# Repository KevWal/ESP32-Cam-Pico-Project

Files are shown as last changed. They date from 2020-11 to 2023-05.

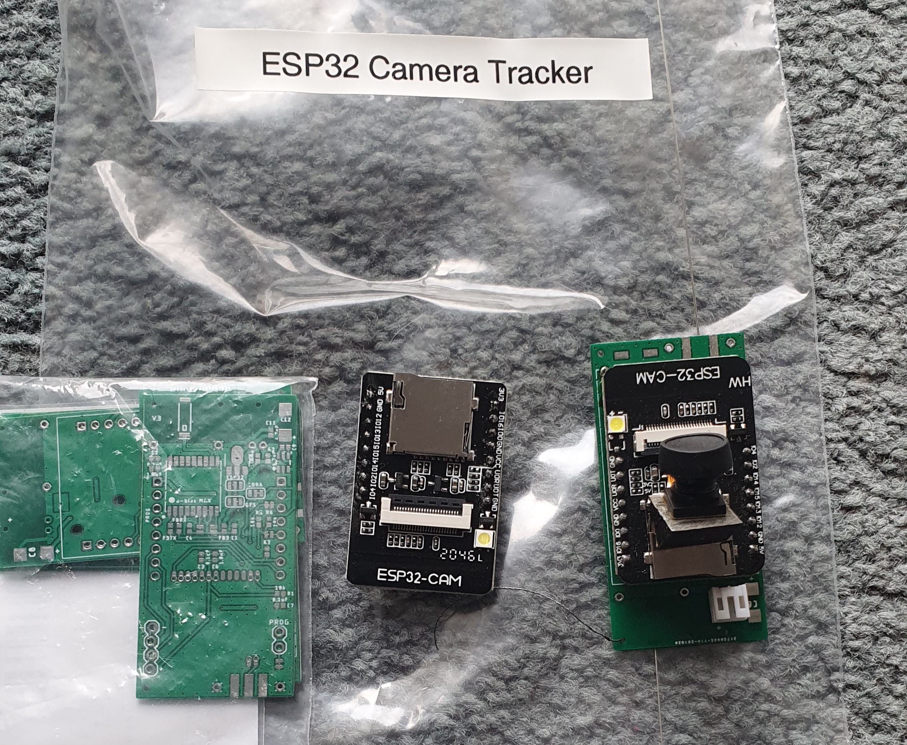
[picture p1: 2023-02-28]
20230218_130314.jpg

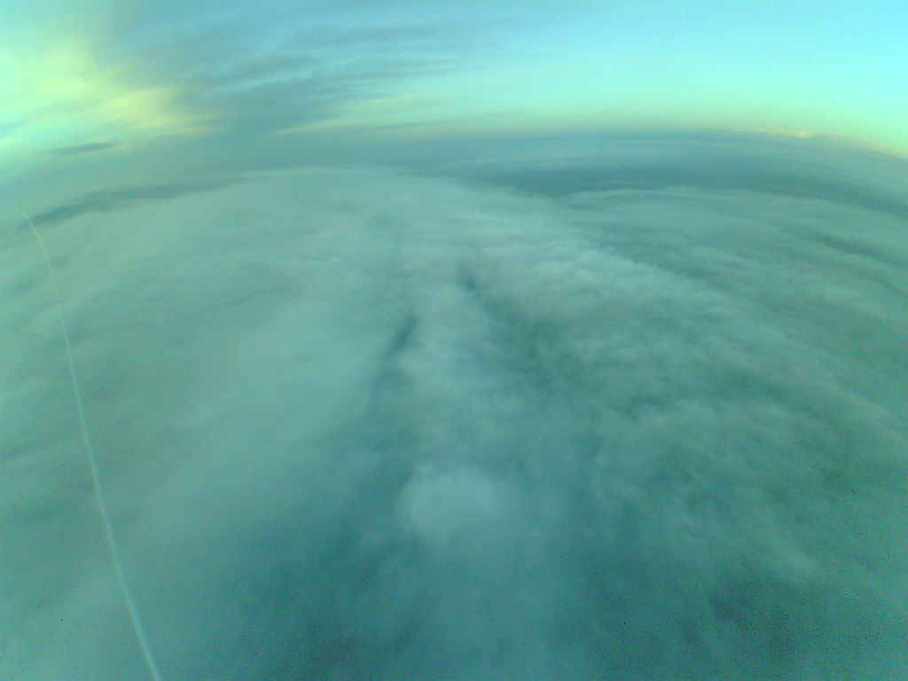
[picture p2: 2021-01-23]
Flight2/2021-01-23--08-14-36-KEW03-2DE02.jpg

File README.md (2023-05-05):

ESP32 Camera Tracker
Written to run on ESP32-Cam board + Lora + GPS

Original code by mkshrps - https://github.com/mkshrps/espcam
Some other ideas from Stuart - https://stuartsprojects.github.io/2020/08/27/ESP32CAM-TrackerAddOn-Board.html

1. Transmits jpg data over lora using SSDV protocol;
2. Interleaves GPS using UKHAS protocol packets;
3. Compatible with PITS LoRa-Gateway receiver.

ESP32-CAM board does not include lora device or GPS device which need to be connected.

Program through the U0R and U0T pins (serial pins) with GPIO0 connected to Gnd.
Debugging output is also on the U0R and U0T pins.

Weights
------
12.4g - Tracker inc 180deg Camera, guitar wire GPS & LoRa Aerial<br>
25g - 3 x AAA soldered together with wire - lasted 14 hours in freezer<br>
21g - 2 x AAA in holder with wire<br>
40g - 2 x AA in holder with wire<br>
14g - 450Ma LiPo<br>

LiPo Version, 26.5g total weight:<br>
1 x Qualtex, 72Ltr Helium, 10g free lift, 0.120m3 unstretched volume, 6,400m burst, 1.7m/sec ascent, 60 mins to burst<br>
2 x Qualtex, 58Ltr Helium each, 10g free lift each, 0.120m3 unstretched volume, 8,400m burst, 1.9m/sec ascent, 75 mins to burst<br>

AA Version, 52.5g total weight:<br>
1 x 100g Pawan, 200ltr Helium, 50g free lift, 20,325m burst, 2.9m/sec ascent, 117mins to burst

AAA Version, 12.5g + 25g = 38g total weight:<br>
1 x Qualtex, 70Ltr Helium, 10g free lift, 0.120m3 unstretched volume, 4,900m burst, 1.7m/sec ascent, 48 mins to burst<br>
2 x Qualtex, 62Ltr Helium each, 10g free lift each, 0.120m3 unstretched volume, 7,500m burst, 1.9m/sec ascent, 65 mins to burst<br>
2 x Chineese, 58Ltr Helium each, 6g free lift each, 0.120m3 unstretched volume, 7,640m burst, 1.9m/sec ascent, 65 mins to float!  42g / 2 = 21g each + 6g = 27g each

Buck version intended for LiPo but used for 3 x AAA

PCB
---

The PCB is designed with many options, mainly around power.  The board is designed to be powered by 2 x AAA or a 3.7v Lipo.  With 2 x AAA I found it needs a boost converter if using the ATGM GPS.  With 1 x 3.7v Lipo I recomend using the buck convertor.  You could use the 3.3v limiting effect of the Boost regulator, but as it is a charge doubler style is uses more current from the battery.

*Flying showed 3 x AAA with a buck convertor is a good option.*

GPS
---
Expects a NMEA GPS, tested with ATGM and UBLOX MAX GPS's

Lora
----
PCB is based on a Dorji DRF1278F LORA module.

Code should support any of the LORA modules listed here:
https://github.com/sandeepmistry/arduino-LoRa

Cameras
-------
Tested with various view angle versions of the OV2640.  This is the standard ESP32 camera.

Some research on other options below.

OV2640 - 1/4" color CMOS UXGA (1600x1200) 2 megapixel image sensor
Used XGA = 1024x768 or VGA = 640x480
https://www.uctronics.com/download/cam_module/OV2640DS.pdf

OV3660 - 3 megapixels
Supports up to FRAMESIZE_QXGA (2048x1536)
https://github.com/espressif/esp32-camera/files/3783752/OV3660_CSP3_DS_1.3_sida.pdf

OV5640 - 1/4" color CMOS QSXGA 5 megapixel image sensor
Supports up to FRAMESIZE_QSXGA (2560x1920)
https://www.uctronics.com/download/Image_Sensor/OV5640_CSP3_DS.pdf

OV7670 - 0.3Mp
Not reasearched due only 0.3Mp!

OV7725 - 
Supports up to FRAMESIZE_VGA (640x480), doesnt support JPEG

OV9650 - Not supported in main repo.
https://www.uctronics.com/index.php/ov9650-13-mega-pixels-camera-module-p-817l.html

NT99141
Supports QVGA (320x240 xskip or crop), VGA(640x480 xskip or crop) and HD (1280x720)

https://github.com/espressif/esp32-camera/tree/master/sensors
Included on github latest:
	#define OV2640_PID     (0x26)
	#define OV3660_PID     (0x36)
	#define OV5640_PID     (0x56)
	#define OV7670_PID     (0x76)
	#define OV7725_PID     (0x77)
	#define OV9650_PID     (0x96)
	#define NT99141_PID     (0x14)

Included in esp32 v1.04:
	#define OV2640_PID     (0x26)
	#define OV3660_PID     (0x36)
	#define OV7725_PID     (0x77)
	#define OV9650_PID     (0x96)

ESP32 Cam module
----------------
https://randomnerdtutorials.com/esp32-cam-ai-thinker-pinout/<br>
https://docs.ai-thinker.com/esp32-cam<br>
https://docs.ai-thinker.com/_media/esp32/docs/esp32_cam_sch.pdf<br>
https://www.espressif.com/sites/default/files/documentation/esp32_technical_reference_manual_en.pdf<br>
https://github.com/espressif/esptool/wiki/ESP32-Boot-Mode-Selection

GPIO32 controls camera power, but if you power the camera down I cant seem to re-initialise it without a reboot (which is now done through a deep sleep reboot)

Arduino IDE
-----------
I added a custom board definition for esp32camkw.upload.speed=921600 to speed uploads.
C:\Users\WALTONK\AppData\Local\Arduino15\packages\esp32\hardware\esp32\1.0.4

Simple Build Notes  - 3 x AA/AAA option
---------------------------------------
Batteries - 3 x AA/AAA = 4.8v down to 2.4v

Reg - MCP170333MB SOT89 or similar<br>
Reg - Add C8, C10, C11 & C12 capacitors

GPS - Tested with ATGM or UBlox Max 3.3v GPS chips<br>
GPS - Add GPS Ferrites and capacitors

Tx - Add Dorji DRF1278F module<br>
Tx - Add R1, C7, C3 and C6<br>
Tx - Set jumper to 3.3v

ESP32 - Add C2, C5, R5 & R6<br>
ESP32 - Remove ESP32 Regulator and Flash transistor<br>
ESP32 - Add ESP32 Camera module to PCB

GPS Antenna - Add chip antenna or 46mm wire (total length)<br>
LoRa Antenna - Add 185mm wire (total length)

Lora Mode
---------
Code setup for:
	Implicit Header (LoRa.beginPacket(1))
	SpreadingFactor(6);
    SignalBandwidth(20.8E3);
    ErrorCodingRate4(5);
    SyncWord(0x12);
    enableCrc();
= Dave Akerman PITS mode 1
https://github.com/PiInTheSky/lora-gateway

Power Consumption
------------------
ESP32 Cam module with regulator removed and flash LED transistor removed<br>
	44ma - Default frequency<br>
	14ma - Reduce to 20Mhz<br>
	14ma - Turn off BT & WIFI<br>
	16ma - Post SPI / Lora Setup<br>
	42ma - Camera setup<br>
	38ma - Disable camera XCLK<br>
	15ma - Turn off camera
	
Board Power Consumption by Frequency, with Lora, GPS and Camera attached but not initialised
	160Mhz, 55ma, 80Mhz, 48ma
	40Mhz, 38ma, 30Mhz, 38ma
	20Mhz, 36ma, 10Mhz, 35ma
	8Mhz, 34ma, 4Mhz, 34ma
	2Mhz, 34ma, 1Mhz, 34ma

ToDo
----
See if we can get Lora and SD Card working together, event though they share pins.  
Stuart did here, but didnt send images: 
https://stuartsprojects.github.io/2020/08/07/ESP32CAM-as-a-Balloon-Tracker-Really!-Copy.html
https://stuartsprojects.github.io/2020/08/27/ESP32CAM-TrackerAddOn-Board.html

Send packets multiple times or auto request resends?

RTTY Code
	Lora library currently in use doesn't appear to have RTTY mode options
	https://github.com/sandeepmistry/arduino-LoRa/blob/master/src/LoRa.cpp
	PITS FSK / RTTY mode details here:
		https://github.com/PiInTheSky/pits/commit/30943ab8ea988695e4e158648f1855fd9fa906bd
		http://www.daveakerman.com/?p=2350
	Stuarts RTTY option here:
		https://github.com/StuartsProjects/Tracker-Library/blob/master/FSK_RTTY2.h
		https://github.com/StuartsProjects/Tracker-Library/blob/master/FSK_RTTY3.h

Add Lora calling frequency tx.

Add use of HabPack binary protocol

Report gps signal quality?
	Base on https://github.com/mikalhart/TinyGPSPlus/blob/master/examples/SatelliteTracker/SatelliteTracker.ino

Record Voltage when taking a picture and send it next telem packet.

PCB
---
Move reset switch hole to be slightly more aligned

Thinner middle pad for buck reg to allow different footprint

Vsupply resister divider on another adc pin too, no solder jumper neeeded.

Increase PCB string holes size, and 4 corner holes to allow vertical down suspension

Lengthen PCB

Different boost converter - current uses lots of current and can't supply enough output current when batteries weak.

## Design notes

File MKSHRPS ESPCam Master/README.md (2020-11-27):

# espcam
esp camera tracker
Written to run on ESPCAM board this project 

1. transmits jpg data over lora using SSDV protocol
2. inerleaves GPS tracking data packets 
3. compatible with PITS Gateway receiver

ESPCAM board does not include lora device or GPS device which need to be connected.

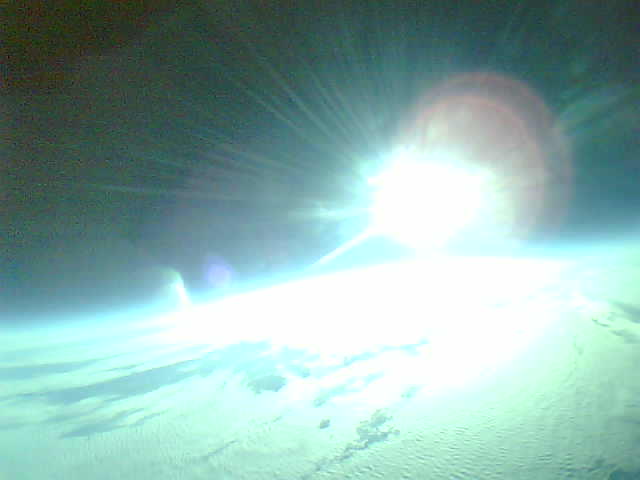
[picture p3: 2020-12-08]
Flight1/2020-12-06--12-41-20-KEW02-2D6B4.jpeg

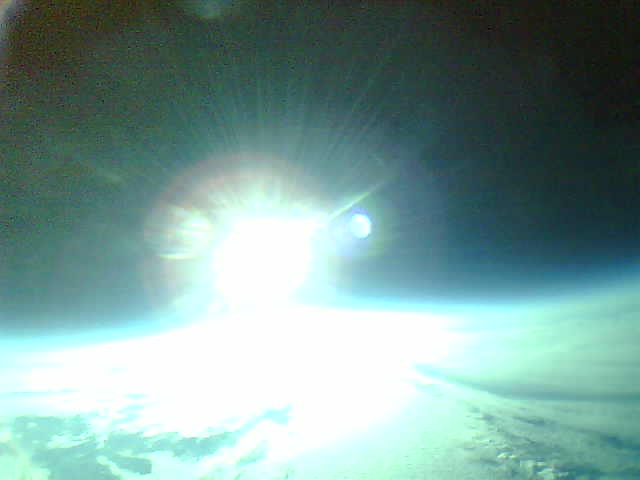
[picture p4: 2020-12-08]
Flight1/2020-12-06--12-49-00-KEW02-2D6B5.jpeg

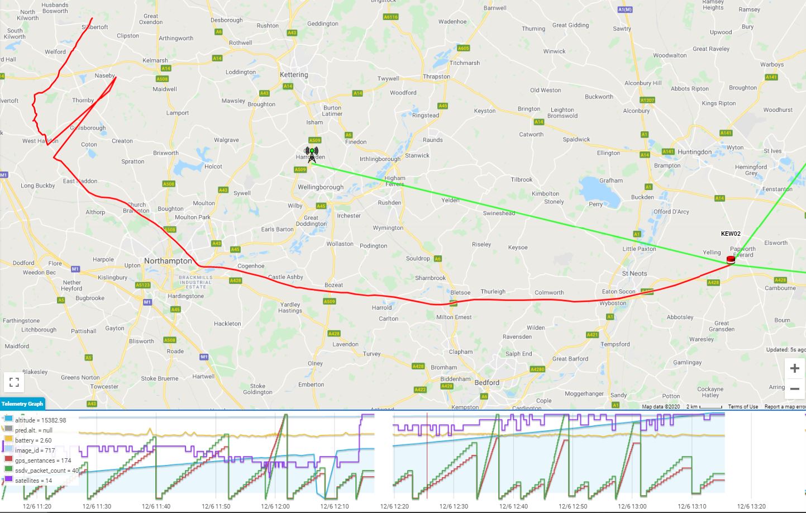
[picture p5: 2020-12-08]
Flight1/Capture3.JPG

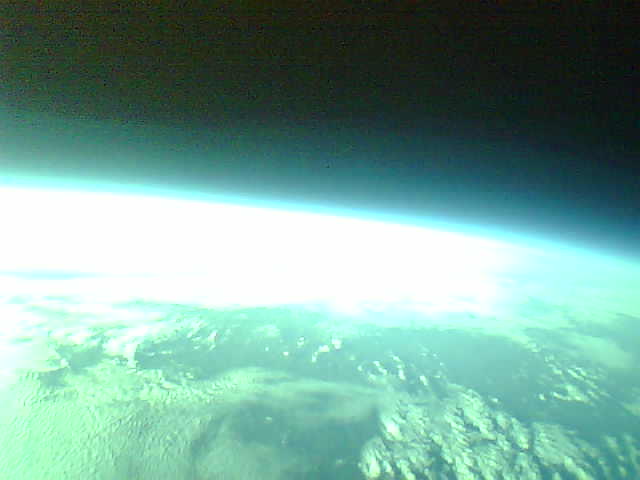
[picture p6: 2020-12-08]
Flight1/2020-12-06--12-52-43-KEW02-2D6B6.jpeg

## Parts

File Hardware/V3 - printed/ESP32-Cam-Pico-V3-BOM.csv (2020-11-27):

Qty | Value | Device | Package | Parts | Description | ARROW_PART_NUMBER | ARROW_PRICE-STOCK | DESCRIPTION | HEIGHT | MANUFACTURER_NAME | MANUFACTURER_PART_NUMBER | MFG_PART | MOUSER_PART_NUMBER | MOUSER_PRICE-STOCK | POPULARITY | PROD_ID | SF_ID | SPICEPREFIX | VALUE
4 |  | 1,6/0,8 | 1,6/0,8 | PAD1, PAD2, PAD3, PAD4 | THROUGH-HOLE PAD |  |  |  |  |  |  |  |  |  | 15
1 |  | CONN_02JST-PTH-2-KIT | JST-2-PTH-KIT | J1 | Multi connection point. Often used as Generic Header-pin footprint for 0.1 inch spaced/style header connections
1 |  | CONN_02LOCK | 1X02_LOCK | J3 | Multi connection point. Often used as Generic Header-pin footprint for 0.1 inch spaced/style header connections
1 |  | CONN_04LOCK | 1X04_LOCK | J2 | Multi connection point. Often used as Generic Header-pin footprint for 0.1 inch spaced/style header connections |  |  |  |  |  |  |  |  |  |  | CONN-09696
2 |  | SMD2 | SMD1,27-2,54 | PAD5, PAD6 | SMD PAD |  |  |  |  |  |  |  |  |  | 15
4 | 0.1uF | 0.1UF-0402-6.3V-10%-X7R | 0402 | C1, C2, C3, C7 | 0.1µF ceramic capacitors |  |  |  |  |  |  |  |  |  |  | CAP-14993 |  |  | 0.1uF
1 | 0k | 10KOHM-0402-1/16W-1% | 0402 | R2 | 10kΩ resistor |  |  |  |  |  |  |  |  |  |  | RES-14241 |  |  | 10k
3 | 1.0uF | 1.0UF-0402-16V-10% | 0402 | C4, C5, C6 | 1µF ceramic capacitors |  |  |  |  |  |  |  |  |  |  | CAP-12417 |  |  | 1.0uF
1 | 1.575GHz | ANTENNAGPS-2X7MM | ANT-GPS-2X7MM | U$2 | Single-ended Antennae |  |  |  |  |  |  |  |  |  |  | ANT-09087 | GPS-09131 |  | 1.575GHz
4 | 10k | 10KOHM-0402-1/16W-1% | 0402 | R1, R5, R6, R7 | 10kΩ resistor |  |  |  |  |  |  |  |  |  |  | RES-14241 |  |  | 10k
2 | 220uF | CPOL-EUSMCC | SMC_C | C8, C12 | POLARIZED CAPACITOR, European symbol |  |  |  |  |  |  |  |  |  | 4 |  |  | C
3 | 4.7uF | 1.0UF-0402-16V-10% | 0402 | C9, C10, C11 | 1µF ceramic capacitors |  |  |  |  |  |  |  |  |  |  | CAP-12417 |  |  | 1.0uF
1 | DRF1278F_2LESS_PINS | DRF1278F_2LESS_PINS | DRF1278F_2_LESS_PINS | U$3
1 | ESP32-CAM | ESP32-CAM | ESP32CAM | IC1 | Modules PCBA Module RoHS |  |  | Modules PCBA Module RoHS | 5mm | Ai-Thinker | ESP32-CAM
3 | FERRITE_BEAD-120_OHM-0402 | FERRITE_BEAD-120_OHM-0402 | 0402 | FB3, FBRX, FBTX | Ferrite Bead (blocks, cores, rings, chokes, etc.) |  |  |  |  |  |  | BLM15HB121SN1D |  |  |  | NDUC-14206
1 | HX4002 | CE021SOT-23 | SOT23-6 | U1 | CE021 |  |  |  |  |  |  |  |  |  |  |  |  |  | HX4002
5 | JUMPER-SMT_2_NC_TRACE_NO-SILK | JUMPER-SMT_2_NC_TRACE_NO-SILK | SMT-JUMPER_2_NC_TRACE_NO-SILK | JP1, JP2, JP6, JP9, JP10 | Normally closed trace jumper
3 | JUMPER-SMT_3_1-NC_TRACE_SILK | JUMPER-SMT_3_1-NC_TRACE_SILK | SMT-JUMPER_3_1-NC_TRACE_SILK | ESP32, GPS, LORA | Normally closed trace jumper (1 of 2 connections)
1 | MAX-M8 | MAX-M8 | MAX-M8 | U$1 | u-blox MAX GNSS module
1 | MCP170333MB | MCP170333MB | SOT89 | IC2 | 250 mA, 16V, Low Quiescent Current LDO Regulator |  |  |  |  |  |  |  |  |  | 0
1 | SMA_EDGE | SMA_EDGE | SMA-EDGE | J$1 | SMA Antenna Connector

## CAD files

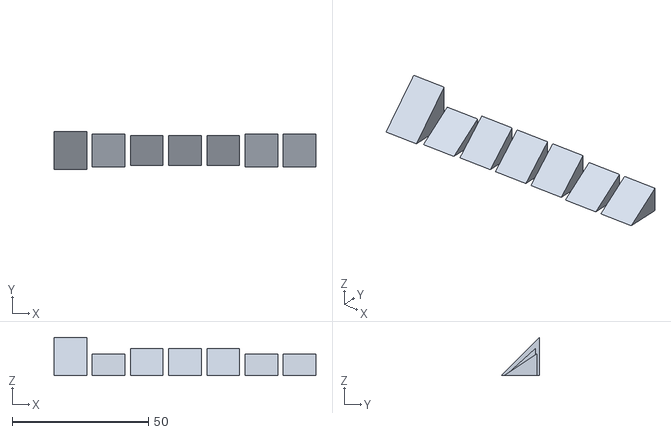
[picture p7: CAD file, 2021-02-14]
CameraWedge/WedgeMulti.stl
96.0 x 14.0 x 14.0

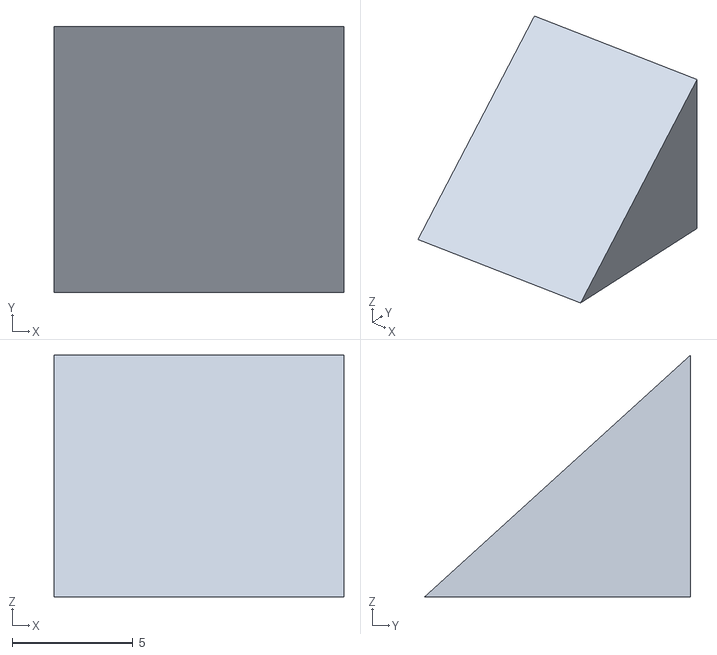
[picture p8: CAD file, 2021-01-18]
CameraWedge/Wedge2.stl
12.0 x 11.0 x 10.0

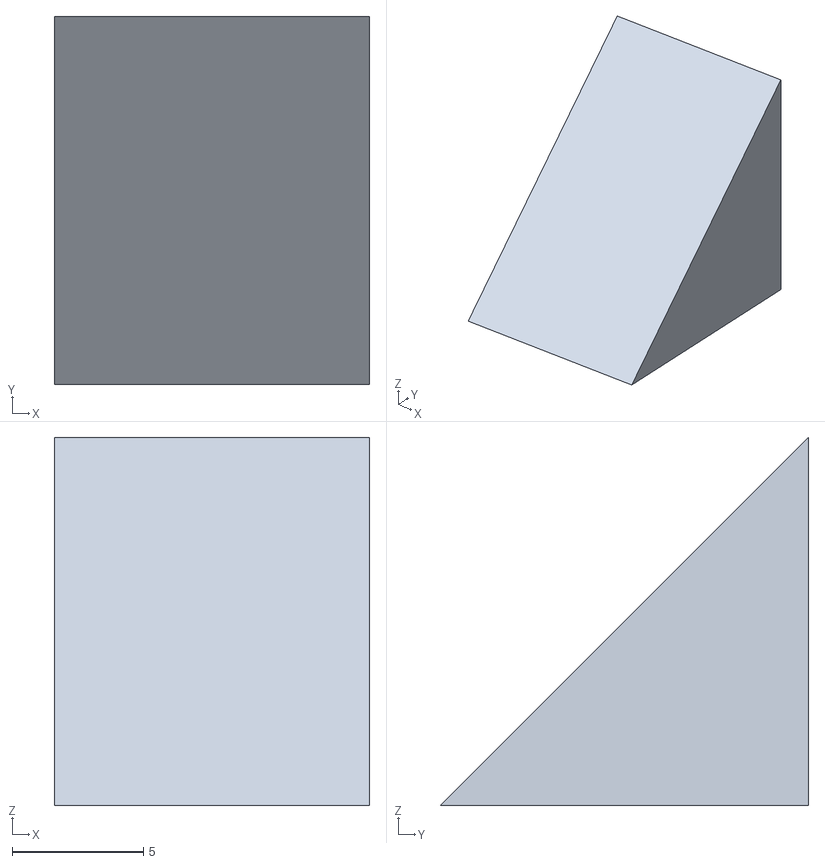
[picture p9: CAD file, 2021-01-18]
CameraWedge/Wedge.stl
12.0 x 14.0 x 14.0

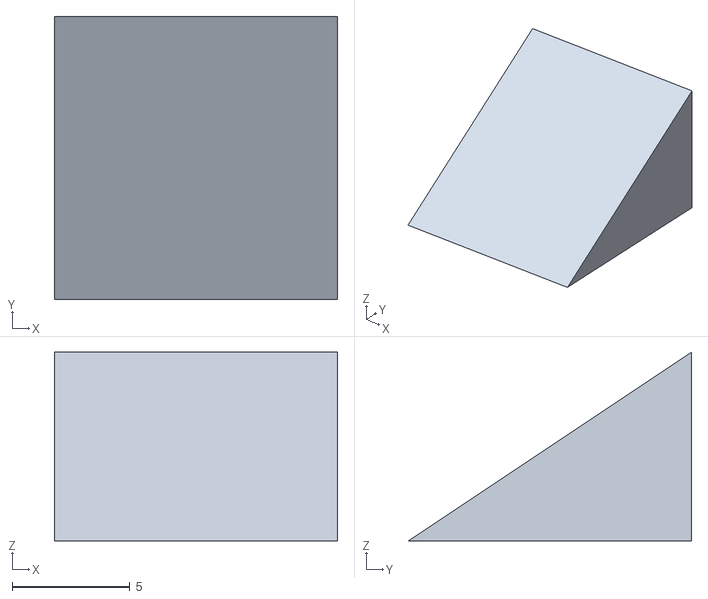
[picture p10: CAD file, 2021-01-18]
CameraWedge/Wedge3.stl
12.0 x 12.0 x 8.00

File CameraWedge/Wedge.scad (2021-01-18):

module prism(l, w, h){
       polyhedron(
               points=[[0,0,0], [l,0,0], [l,w,0], [0,w,0], [0,w,h], [l,w,h]],
               faces=[[0,1,2,3],[5,4,3,2],[0,4,5,1],[0,3,4],[5,2,1]]
               );
       
       // preview unfolded (do not include in your function
       z = 0.08;
       separation = 2;
       border = .2;
       //translate([0,w+separation,0])
       //    cube([l,w,z]);
       //translate([0,w+separation+w+border,0])
       //    cube([l,h,z]);
       //translate([0,w+separation+w+border+h+border,0])
       //    cube([l,sqrt(w*w+h*h),z]);
       //translate([l+border,w+separation+w+border+h+border,0])
       //    polyhedron(
       //            points=[[0,0,0],[h,0,0],[0,sqrt(w*w+h*h),0], [0,0,z],[h,0,z],[0,sqrt(w*w+h*h),z]],
       //            faces=[[0,1,2], [3,5,4], [0,3,4,1], [1,4,5,2], [2,5,3,0]]
       //            );
       //translate([0-border,w+separation+w+border+h+border,0])
       //    polyhedron(
       //            points=[[0,0,0],[0-h,0,0],[0,sqrt(w*w+h*h),0], [0,0,z],[0-h,0,z],[0,sqrt(w*w+h*h),z]],
       //            faces=[[1,0,2],[5,3,4],[0,1,4,3],[1,2,5,4],[2,0,3,5]]
       //            );
       }
   
   prism(12, 12, 8);

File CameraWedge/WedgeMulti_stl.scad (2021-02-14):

translate([42.0, 89.0, -0.0])rotate([0, 0, 0])translate([-6.0, -7.0, 0])import("C:\Users\WALTONK\Documents\ESP32 Cam Pico Project\CameraWedge\Wedge.stl");
translate([56.0, 89.0, -0.0])rotate([0, 0, 0])translate([-6.0, -6.0, 0])import("C:\Users\WALTONK\Documents\ESP32 Cam Pico Project\CameraWedge\Wedge3.stl");
translate([70.0, 89.0, -0.0])rotate([0, 0, 0])translate([-6.0, -5.5, 0])import("C:\Users\WALTONK\Documents\ESP32 Cam Pico Project\CameraWedge\Wedge2.stl");
translate([84.0, 89.0, -0.0])rotate([0, 0, 0])translate([-6.0, -5.5, 0])import("C:\Users\WALTONK\Documents\ESP32 Cam Pico Project\CameraWedge\Wedge2.stl");
translate([98.0, 89.0, -0.0])rotate([0, 0, 0])translate([-6.0, -5.5, 0])import("C:\Users\WALTONK\Documents\ESP32 Cam Pico Project\CameraWedge\Wedge2.stl");
translate([112.0, 89.0, -0.0])rotate([0, 0, 0])translate([-6.0, -6.0, 0])import("C:\Users\WALTONK\Documents\ESP32 Cam Pico Project\CameraWedge\Wedge3.stl");
translate([126.0, 89.0, -0.0])rotate([0, 0, 0])translate([-6.0, -6.0, 0])import("C:\Users\WALTONK\Documents\ESP32 Cam Pico Project\CameraWedge\Wedge3.stl");

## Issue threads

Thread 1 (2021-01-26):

README formatting

matburnham, 2021-01-26:
Looks like the README could do with better markdown formatting, or not actually having a Markdown extension so that it doesn't get formatted a Markdown.

e.g. the Power Consumption section is a tad difficult to read when GitHub renders the Markdown:
`
ESP32 Cam module, regulator removed and flash LED transistor removed 44ma - Default frequency 14ma - Reduce to 20Mhz 14ma - Turn off BT & WIFI 16ma - Post SPI / Lora Setup 42ma - Camera setup 38ma - Disable camera XCLK 15ma - Turn off camera
`

The raw file is much more readable:
```
ESP32 Cam module, regulator removed and flash LED transistor removed
	44ma - Default frequency
	14ma - Reduce to 20Mhz
	14ma - Turn off BT & WIFI
	16ma - Post SPI / Lora Setup
	42ma - Camera setup
	38ma - Disable camera XCLK
	15ma - Turn off camera
```

KevWal, 2023-05-05:
Mostly sorted!

Closed 2023-05-05.

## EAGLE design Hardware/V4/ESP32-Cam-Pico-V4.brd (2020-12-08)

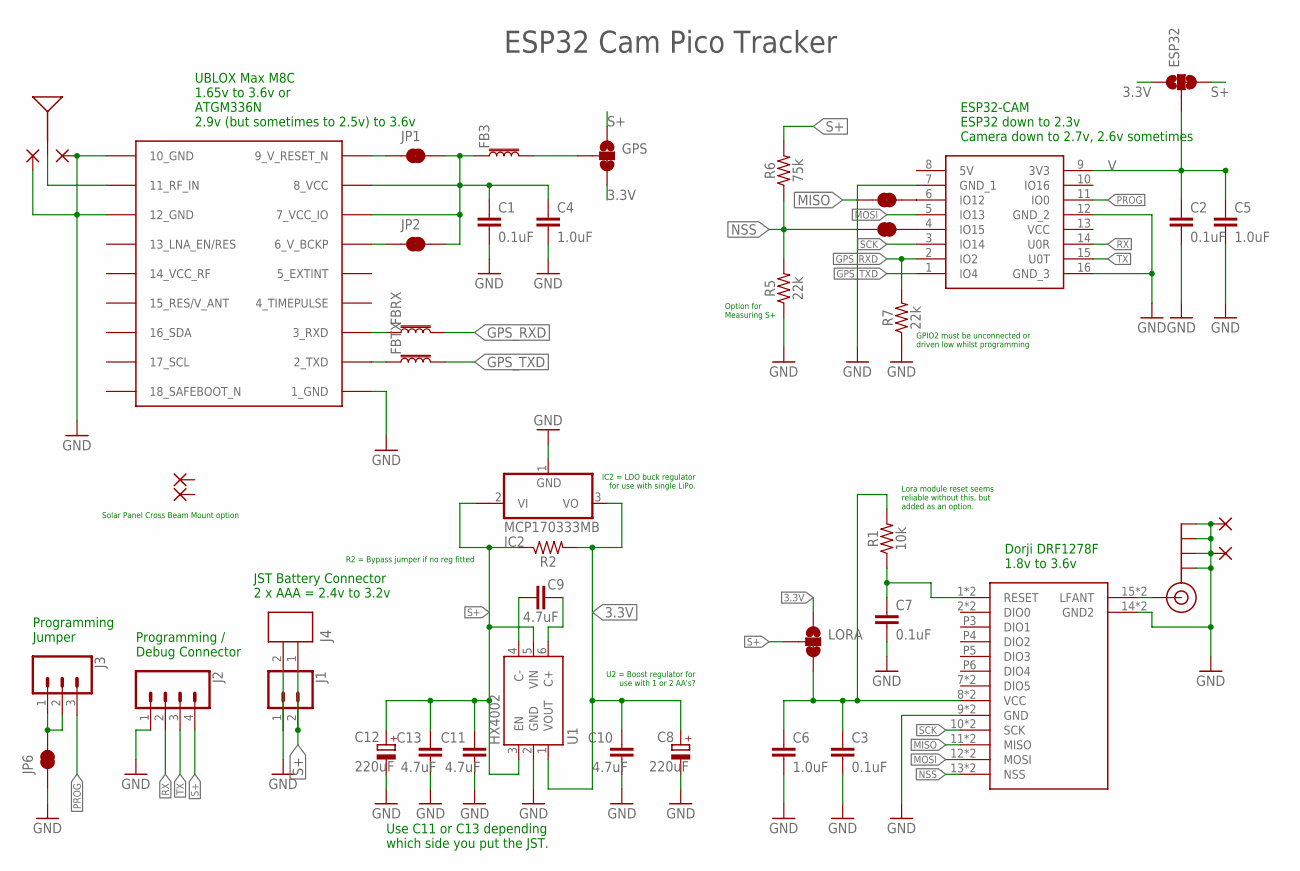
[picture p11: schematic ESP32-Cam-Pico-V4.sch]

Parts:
C1, C2, C3, C7: 0.1uF; 0402
C4, C5, C6: 1.0uF; 0402
C8, C12: 220uF; SMC_C
C9, C10, C11, C13: 4.7uF; 0402
ESP32: JUMPER-SMT_3_1-NC_TRACE_SILK; SMT-JUMPER_3_1-NC_TRACE_SILK
FB3: FERRITE_BEAD-120_OHM-0402; 0402
FBRX: FERRITE_BEAD-120_OHM-0402; 0402
FBTX: FERRITE_BEAD-120_OHM-0402; 0402
GPS: JUMPER-SMT_3_1-NC_TRACE_SILK; SMT-JUMPER_3_1-NC_TRACE_SILK
IC1: ESP32-CAM; ESP32CAM
IC2: MCP170333MB; SOT89
J1: CONN_02JST-PTH-2-KIT; JST-2-PTH-KIT
J2: CONN_04LOCK; 1X04_LOCK
J3: CONN_03LOCK; 1X03_LOCK
J4: JST_ZH_2PIN
J$1: SMA_EDGE; SMA-EDGE
JP1, JP2, JP6, JP9, JP10: JUMPER-SMT_2_NC_TRACE_NO-SILK; SMT-JUMPER_2_NC_TRACE_NO-SILK
LORA: JUMPER-SMT_3_1-NC_TRACE_SILK; SMT-JUMPER_3_1-NC_TRACE_SILK
PAD1, PAD2, PAD3, PAD4: 1,6/0,8
PAD5, PAD6: SMD2; SMD1,27-2,54
R1: 10k; 0402
R2: 0k; 0402
R5, R7: 22k; 0402
R6: 75k; 0402
U1: HX4002; SOT23-6
U$1: MAX-M8
U$2: 1.575GHz; ANT-GPS-2X7MM
U$3: DRF1278F_2LESS_PINS; DRF1278F_2_LESS_PINS

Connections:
3.3V: C8.+, C10.1, ESP32.1, GPS.3, IC2.3 (VO), LORA.1, R2.2, U1.1 (VOUT)
ANT: J$1.SIG (SIGNAL), U$3.15 (LFANT), U$3.P15 (LFANT)
GND: C1.2, C2.2, C3.2, C4.2, C5.2, C6.2, C7.2, C8.-, C10.2, C11.2, C12.-, C13.2, IC1.7 (GND_1), IC1.12 (GND_2), IC1.16 (GND_3), IC2.1 (GND), J1.1, J2.1, J4.2, J$1.GND@0 (GND), J$1.GND@1 (GND), J$1.GND@2 (GND), J$1.GND@3 (GND), JP6.1, PAD1.1, PAD2.1, PAD3.1, PAD4.1, R5.1, R7.1, U1.2 (GND), U$1.1_GND, U$1.10_GND, U$1.12_GND, U$3.9 (GND), U$3.14 (GND2), U$3.P9 (GND), U$3.P14 (GND2)
GPS_RXD: FBRX.2, IC1.2 (IO2), R7.2
GPS_TXD: FBTX.2, IC1.1 (IO4)
MISO: JP9.1, U$3.11 (MISO), U$3.P11 (MISO)
MOSI: IC1.5 (IO13), U$3.12 (MOSI), U$3.P12 (MOSI)
unnamed: U$1.11_RF_IN, U$2.1
unnamed: FBRX.1, U$1.3_RXD
unnamed: FBTX.1, U$1.2_TXD
unnamed: JP1.1, U$1.9_RESET_N (9_V_RESET_N)
unnamed: JP2.1, U$1.6_V_BCKP
unnamed: C7.1, R1.1, U$3.1 (RESET), U$3.P1 (RESET)
unnamed: FB3.2, GPS.2
unnamed: C1.1, C4.1, FB3.1, JP1.2, JP2.2, U$1.7_VCC_IO, U$1.8_VCC
unnamed: C9.2, U1.4 (C-)
unnamed: J3.1, J3.2, JP6.2
unnamed: C9.1, U1.6 (C+)
unnamed: IC1.6 (IO12), JP9.2
unnamed: IC1.4 (IO15), JP10.2
NSS: JP10.1, R5.2, R6.1, U$3.13 (NSS), U$3.P13 (NSS)
PROG: IC1.11 (IO0), J3.3
RX: IC1.14 (U0R), J2.2
S+: C3.1, C6.1, C11.1, C12.+, C13.1, ESP32.3, GPS.1, IC2.2@1 (VI1), J1.2, J2.4, J4.1, LORA.2, LORA.3, R1.2, R2.1, R6.2, U1.3 (EN), U1.5 (VIN), U$3.8 (VCC), U$3.P8 (VCC)
SCK: IC1.3 (IO14), U$3.10 (SCK), U$3.P10 (SCK)
TX: IC1.15 (U0T), J2.3
V: C2.1, C5.1, ESP32.2, IC1.9 (3V3)

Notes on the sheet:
JST Battery Connector 2 x AAA = 2.4v to 3.2v
Programming / Debug Connector
Programming Jumper
UBLOX Max M8C 1.65v to 3.6v or ATGM336N 2.9v (but sometimes to 2.5v) to 3.6v
Dorji DRF1278F 1.8v to 3.6v
ESP32-CAM ESP32 down to 2.3v Camera down to 2.7v, 2.6v sometimes
ESP32 Cam Pico Tracker
Lora module reset seems reliable without this, but added as an option.
R2 = Bypass jumper if no reg fitted
Option for Measuring S+
IC2 = LDO buck regulator for use with single LiPo.
U2 = Boost regulator for use with 1 or 2 AA's?
GPIO2 must be unconnected or driven low whilst programming
Solar Panel Cross Beam Mount option
Use C11 or C13 depending which side you put the JST.

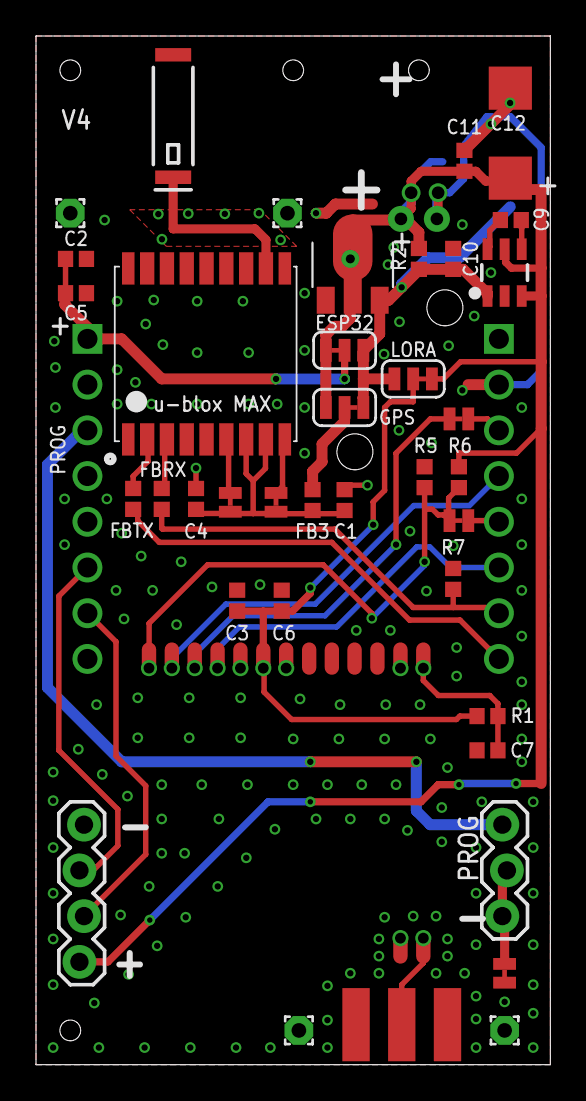
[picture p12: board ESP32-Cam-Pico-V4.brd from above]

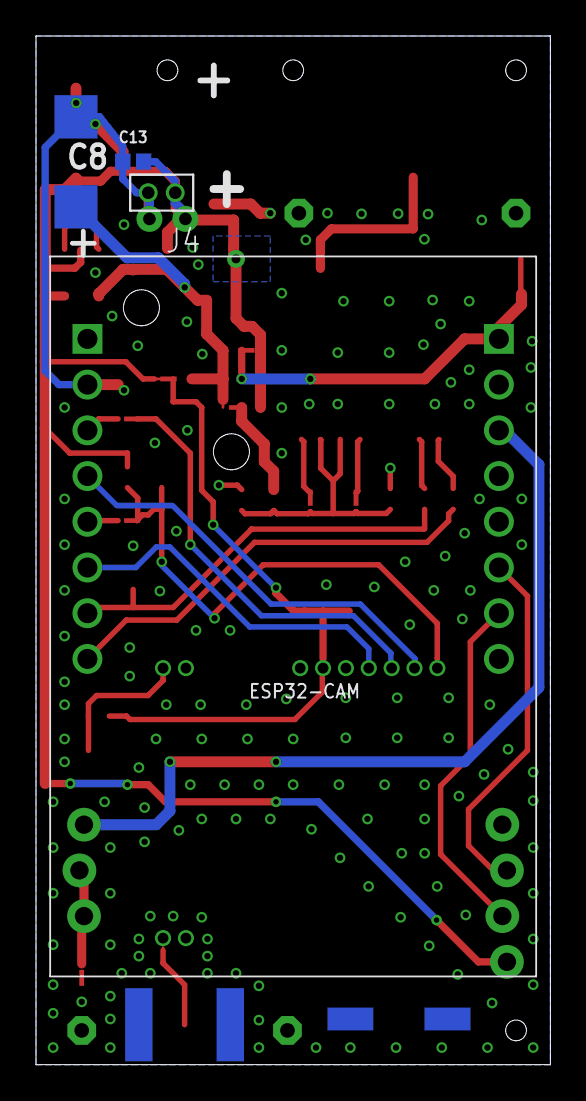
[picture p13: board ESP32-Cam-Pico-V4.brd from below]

Board: 2 copper layers, 28.6 x 57.1 mm, 46 parts (7 on the bottom side), 27 nets.

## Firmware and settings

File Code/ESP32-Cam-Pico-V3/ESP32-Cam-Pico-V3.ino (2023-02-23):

/*
 * ESP32 Camera Tracker
 * Written to run on ESPCam board + Lora + GPS
 * 
 * Original code by mkshrps - https://github.com/mkshrps/espcam
 * 
 * Modified Kevin Walton - https://github.com/KevWal
*/

// Specify how many times we send each image packet.
// High values take more time to send an image but less risk of missing packets
#define PACKETS 2

// transmit a telemetry packet every X SSDV packets
#define INTERLEAVE_TELEM            8

// Specify the power configuration
// BUCK assumes that all components are powered by the buck regulator, and that a 3.2v lipo cell or 3 x AAA's are used.
// BOOST assumes a 3.3v boost regulator powers the ESP32-CAM and the GPS module (DRF module ok down to 1.8v)
// NONE assumes 2 x AAA batteries power all components, and the board uses a UBLOX MAX 8C GPS module (1.65v min)
//#define BOOST
#define BUCK
//#define NONE

#ifdef BOOST
  #define CALLSIGN "KEW02"          // Set your balloon callsig, max 6 characters
  long frq = 434720000;             // Set transmit frequency, xx on my gateway
#elif defined(BUCK)
  #define CALLSIGN "KEW03"
  long frq = 434730000;             //434.738,0 on my gateway
#elif defined(NONE)
  #define CALLSIGN "KEW01"
  long frq = 434710000;             // xx on my gateway
#endif
// IR2030/1/10 433.05-434.79 MHz 10 mW e.r.p. Duty cycle limit 10% or
// IR2030/1/12 433.04-434.79 MHz 10 mW e.r.p. Channel Spacing <= 25 kHz
// 434.5 to 435 is Scandanavia repeater output

//================================================================================


// Edit Wifi ssid & password
//#define SSID "NSA"
//#define PASSWORD "orange"

#define LORA_CSS  15   // Lora CSS GPIO - will be 2,4 or 15 (Standard HSPI = 15) 
#define CORE_FREQ  20  // Mhz, reduced to save power.  20Mhz seems to be the sweet spot, 10mhz stops Lora module working

#include <SPI.h>
#include <WiFi.h>
#include <Preferences.h>
#include "driver/adc.h"
#include <esp_wifi.h>
#include <esp_bt.h>
//#include "esp_pm.h"
//#include "soc/soc.h"
#include "soc/rtc_cntl_reg.h"
#include "esp.h"
#include <esp_camera.h>

// Forward declare cam clock stop/start and (depreciated) temperature read. 
extern "C" {
esp_err_t camera_enable_out_clock(camera_config_t *config);
void camera_disable_out_clock();
uint8_t temprature_sens_read();
}

#include <LoRa.h>      // Install from https://github.com/sandeepmistry/arduino-LoRa or "LoRa" by Sandeep Mistry in Library Manager
#include <TinyGPS++.h> // Install from http://arduiniana.org/libraries/tinygpsplus/ or TinyGPSPlus by Mikal Hart in Library Manager
#include <ssdv.h>      // Install from https://github.com/fsphil/ssdv

// Time
//#include <time.h>           // ESP32 native time library - graceful NTP server synchronization
//#include <lwip/apps/sntp.h> // ESP32 Lightweight IP SNTP client API
//#include <lwip/err.h>       // ESP32 Lightweight IP errors

// MicroSD definitions
//#include <driver/sdmmc_host.h>
//#include <driver/sdmmc_defs.h>
//#include <sdmmc_cmd.h>
//#include <esp_vfs_fat.h>

#define SerialDebug Serial    // Nice names for Serial ports
#define SerialGPS Serial2

#include "ESP32-Cam-GPS.h" // Our GPS data structure and GPS routines

// The Preferences object, used to store things in EEPROM
Preferences preferences;

// The TinyGPS++ object
TinyGPSPlus gps;

// ssdv definitions
unsigned int SSDV_quality;

#define IMG_BUFF_SIZE               128   // size of the buffer feeding SSDV process
#define LORA_BUFFER                 255   // size of the lora packet buffer

// CAMERA_MODEL_AI_THINKER
#define PWDN_GPIO_NUM     32 //
#define RESET_GPIO_NUM    -1
#define XCLK_GPIO_NUM      0 //
#define SIOD_GPIO_NUM     26
#define SIOC_GPIO_NUM     27
#define Y9_GPIO_NUM       35
#define Y8_GPIO_NUM       34
#define Y7_GPIO_NUM       39
#define Y6_GPIO_NUM       36
#define Y5_GPIO_NUM       21
#define Y4_GPIO_NUM       19
#define Y3_GPIO_NUM       18
#define Y2_GPIO_NUM        5
#define VSYNC_GPIO_NUM    25
#define HREF_GPIO_NUM     23
#define PCLK_GPIO_NUM     22 //

// Global Variables
//long current_millis;
//long last_capture_millis = 0;
static esp_err_t cam_err = -1;
camera_config_t my_cam_config;
//bool internet_connected = false;
//struct tm timeinfo;
uint8_t imgBuff[IMG_BUFF_SIZE];
uint8_t loraBuff[LORA_BUFFER + 1];
char gpsMessage[256];
uint16_t imageID = 0;
RTC_DATA_ATTR unsigned int gpsMessageCnt = 0; // GPS Message Number for HabHub Sentance ID, saved in memory that survives a deep sleep, but not a power cycle.
uint16_t ssdvPacketCount = 0;

// Time and SSDV objects
//time_t now;
ssdv_t ssdv;

int readV() {
  int Vcc = analogReadMilliVolts(LORA_CSS)*2115/1000-540; // This one uses the calibration but was not in previous release

 /*  If you dont have analogReadMilliVolts use the below
  // analogRead() results vary depending on supply voltage source as GPIO15 has an internal pull up.
  // Divide by 1000 to allow integer maths
#if defined(BOOST)
  int Vcc = ((analogRead(LORA_CSS)*4908/1000)-4513); // tested with Supply of 2.3v to 4.8v with reg @3.3v.
  //SerialDebug.println("  Boost Regulator.");
#elif defined (BUCK)
  int raw = analogRead(LORA_CSS);
  int Vcc = (0.0035*raw*raw) - (6.0911*raw) + 5000; // tested with Supply of 2.3v to 5.0v with reg @3v.
  // y = 0.0035*x*x - 6.0911*x + 5000
  //SerialDebug.println("  Buck Regulator.");
#elif defined(NONE)
  int Vcc = ((analogRead(LORA_CSS)*1744/1000)+566); // tested with Supply of 2.4v to 4.9v with no reg
  //SerialDebug.println("  No Regulator.");
#endif
 */

  pinMode(LORA_CSS, OUTPUT); // Set pin back to an output for SPI / Lora
 
  return Vcc;
}

// Read Camera Buffer
int iread(uint8_t *buffer,int numBytes,camera_fb_t *fb, int fbIndex ){
  int bufSize = 0;
  // have we reached past end of imagebuffer
  if((fbIndex + numBytes ) < fb->len) {
    bufSize = numBytes;
  }  else  {
    bufSize = fb->len - fbIndex;
  }
  // clear the dest buffer
  memset(buffer,0,numBytes);
  memcpy(buffer,&fb->buf[fbIndex],bufSize);
  return bufSize;
}


// Read GPS data
void checkGps(){
  //SerialDebug.println("checkGps()");
  
  while (SerialGPS.available() > 0){  
    gps.encode(SerialGPS.read()); 
  }

  if (!GPS.isValid) {  // If we havent yet had a valid GPS signal, check if it is valid yet
    if (gps.location.isValid() && gps.altitude.isValid() && gps.time.isValid()){
      GPS.isValid = true; // We now have an initial valid GPS signal
    }
  }

}


// Int to Hex
char Hex(uint8_t index)
  {
    char HexTable[] = "0123456789ABCDEF";
    
    return HexTable[index];
  }


// Build HabHub Position Message including CRC
void buildPITSMessage(){
  char tempStr[50];
  
  SerialDebug.println("buildPITSMessage()");
  SerialDebug.printf("  Sats: %d, Sentences passed: %d, Sentences failed: %d\n", gps.satellites.value(), gps.passedChecksum(), gps.failedChecksum());

  gpsMessageCnt++; // Everytime we build a message, build it with a new id.

  // Get data from GPS
  if (gps.location.isValid()){
    GPS.Longitude = (float) gps.location.lng();
    GPS.Latitude = (float) gps.location.lat();
  }
  
  if (gps.altitude.isValid()){
    GPS.Altitude = (long) gps.altitude.meters();
  }
  
  if(gps.time.isValid()){
    GPS.Hours = (uint8_t) gps.time.hour();
    GPS.Minutes = (uint8_t) gps.time.minute();
    GPS.Seconds = (uint8_t) gps.time.second();
  }

  GPS.Speed = gps.speed.value();
  GPS.Direction = gps.course.deg();
  GPS.Satellites = gps.satellites.value();
  
  // If gps data is all ready
  if (gps.location.isValid() && gps.altitude.isValid() && gps.time.isValid() ){
    SerialDebug.println("  GPS location, altitude and time valid.");
  } else {
    SerialDebug.println("  Error: PITS message built, but GPS location, altitude or time not yet valid.");
  }
      
  // $$ ID, count, HH:MM:SS, lat, lng, alt, Speed, Heading, sats, mV, passedChecksum, imageID, ssdvPacketCount
  strcpy(gpsMessage, "$$");
  strcat(gpsMessage, CALLSIGN);
      
  snprintf(tempStr,sizeof(tempStr),",%d,%02d:%02d:%02d,",gpsMessageCnt,GPS.Hours,GPS.Minutes,GPS.Seconds);
  strcat(gpsMessage,tempStr);
      
  // dtostrf() converts float or double
  dtostrf(GPS.Latitude,2,6,tempStr);
  strcat(gpsMessage,tempStr);

  dtostrf(GPS.Longitude,2,6,tempStr);
  strcat(gpsMessage,",");
  strcat(gpsMessage,tempStr);

  ltoa(GPS.Altitude,tempStr,10);
  strcat(gpsMessage,",");
  strcat(gpsMessage,tempStr);

  snprintf(tempStr,40,",%d,%d,%d,%d,%d,%d,%d",GPS.Speed,GPS.Direction,GPS.Satellites,readV(),gps.passedChecksum(),imageID,ssdvPacketCount);
    // Temperature sensor not avaliable on newer hardware
  strcat(gpsMessage,tempStr);

  //KW TODO - what other data can we add here?  sat signal quality etc.
      
  int Count = strlen(gpsMessage);

  // Calculate CRC and append to message
  unsigned int CRC = 0xffff;           // Seed
  for (int i = 2; i < Count; i++){   
      CRC ^= (((unsigned int)gpsMessage[i]) << 8);
      for (uint8_t j=0; j<8; j++) {
          if (CRC & 0x8000)
              CRC = (CRC << 1) ^ 0x1021; // xPolynomial
          else
              CRC <<= 1;
      }
  }

  gpsMessage[Count++] = '*';
  gpsMessage[Count++] = Hex((CRC >> 12) & 15);
  gpsMessage[Count++] = Hex((CRC >> 8) & 15);
  gpsMessage[Count++] = Hex((CRC >> 4) & 15);
  gpsMessage[Count++] = Hex(CRC & 15);
  gpsMessage[Count++] = '\n';  
  gpsMessage[Count++] = '\0';
  
  SerialDebug.println(gpsMessage);
  }


// Main routine
void process_ssdv(camera_fb_t *fb){
  SerialDebug.println("process_ssdv()");

  int index = 0, c = 0;
  ssdvPacketCount = 0;
  
  // initialise ssdv config structure
  ssdv_enc_init(&ssdv, SSDV_TYPE_NOFEC, CALLSIGN, imageID++, SSDV_quality); //Lora inc FEC, so no point having in SSDV Lib
  // SSDV_TYPE_NORMAL or SSDV_TYPE_NOFEC // Cant turn Lora CRC off as Hab gateway assumes it is on, so no point in FEC inside SSDV
  
  // Save the new image ID in EEPROM, so that if we reboot we start from the next image ID
  preferences.putUInt("imageID", imageID);
  
  // set the output lora packet buffer for ssdv where the final ssdv packet will end up
  ssdv_enc_set_buffer(&ssdv, loraBuff);

  while(1){ // Only exits when a full image is sent or the SSDV library gives an error
    checkGps();

    SerialDebug.printf("  Sec: %d, Sats: %d, S passed: %d, S failed: %d, mV: %d.\n", 
                      (int)millis()/1000, gps.satellites.value(), gps.passedChecksum(), gps.failedChecksum(), readV());
    
    // Test to see if Location Packet is to be sent // Change to time based?
    if((ssdvPacketCount % INTERLEAVE_TELEM) == 0){
      buildPITSMessage();
      delay(10);
      LoRa.beginPacket(1);                             // initialise implicit/explicit mode and reset FIFO
      LoRa.write((const uint8_t *)gpsMessage, sizeof(gpsMessage));     // load data into FIFO
      LoRa.endPacket(0);                                // execute transmission, return once complete
      
      // todo Has the GPS position changed, if not do a reboot

/*
      // Test code for no GPS
      delay(10);
      LoRa.beginPacket(1);
      LoRa.write((const uint8_t *)"$$KEW00,217,21:20:43,52.323616,-0.708233,-1,1319,283,4,0,0,0,0*E112",67);
      LoRa.endPacket(0);
*/      
    } // Send Location Packet  
    

    // If the Camera is ok then encode and send image packets
    if (cam_err == ESP_OK) { //ESP_OK
      // Feed the SSDV encoder the image.  Encoder saves it to loraBuff 
      while((c = ssdv_enc_get_packet(&ssdv)) == SSDV_FEED_ME) {
        //size_t r = fread(imageBuffer, 1, 128, fin);
        //SerialDebug.print("read into buffer");
        // read packet worth of bytes from image buffer
        index += iread(imgBuff, IMG_BUFF_SIZE, fb, index);
        SerialDebug.printf("  Feeding SSDV Encoder, index = %d\n", index);

        // ssdv =  struct, imageBuffer = buffer containing image packet, r = size
        ssdv_enc_feed(&ssdv, imgBuff, IMG_BUFF_SIZE);
        //SerialDebug.println(" bfed ");
      }
    
      if(c == SSDV_EOI) {
        SerialDebug.println("  SSDV End of Image");
        break; // Return to main()
      }
      else if(c != SSDV_OK){
        SerialDebug.println("  ERROR: SSDV Error");
        break; // Return to main()
      }

      // move lora data backwards 1 byte This seems needed for pits gateway to read it. (TT7)
      for(uint16_t i = 0; i < 256; i++) {
        loraBuff[i] = loraBuff[i+1]; //KW TODO sort warning: iteration 255u invokes undefined behavior
      }

      // Send each packet multiple times
      for(byte i = 0; i < PACKETS; i++) {
        // Lora transmit image packet
        SerialDebug.printf("  Packet sending: %d.\n", ssdvPacketCount);
        delay(10);
        LoRa.beginPacket(1);          // initialise implicit mode and reset FIFO
        LoRa.write(loraBuff, LORA_BUFFER);     // load data into FIFO
        LoRa.endPacket();             // execute transmission return once complete
      }
      
    } else {// if (cam_err == ESP_OK)
      delay(500); // dont go around the loop so quickly if we are not transmitting SSDV packets
    }

    ssdvPacketCount++; // Increment ssdvPacketCount even if the camera is not ok, otherwise we wont hit INTERLEAVE_TELEM

    if (ssdvPacketCount > 300) {
      SerialDebug.println("  ERROR: ssdvPacketCount > 300");
      break; // incase we get stuck in this loop, for example when the camera isn't on
    }
    
  } // while (1)
}

/* // Init Wifi
bool init_wifi() {
  uint8_t connAttempts = 0;
  SerialDebug.printf("  Connecting to: %s\n", SSID);
  WiFi.begin(SSID, PASSWORD);
  while (WiFi.status() != WL_CONNECTED ) {
    delay(500);
    SerialDebug.print(".");
    if (connAttempts > 10) return false;
    connAttempts++;
  }
  return true;
} */

/*
 // Init the time
void init_time() {
  char sntpservername[] = "pool.ntp.org"; // Needed to resolve ISO C++ forbids converting a string constant to 'char*' error
  sntp_setoperatingmode(SNTP_OPMODE_POLL);
  sntp_setservername(0, sntpservername);
  sntp_init();
*/

/*  Don't wait for time to be set
  // wait for time to be set
  timeinfo = { 0 };
  uint8_t retry = 0;
  const int retry_count = 10;

  while (timeinfo.tm_year < (2016 - 1900) && ++retry < retry_count) {
    SerialDebug.printf("Waiting for system time to be set... (%d/%d)\n", retry, retry_count);
    delay(2000);
    time(&now);
    localtime_r(&now, &timeinfo);
  }
}
*/

/* //Init the SD Card
esp_err_t init_sdcard() {
  esp_err_t ret = ESP_FAIL;
  sdmmc_host_t host = SDMMC_HOST_DEFAULT();
  sdmmc_slot_config_t slot_config = SDMMC_SLOT_CONFIG_DEFAULT();
  esp_vfs_fat_sdmmc_mount_config_t mount_config = {
    .format_if_mount_failed = false,
    .max_files = 1,
  };
  sdmmc_card_t *card;

  SerialDebug.print("  Mounting SD card...");
  ret = esp_vfs_fat_sdmmc_mount("/sdcard", &host, &slot_config, &mount_config, &card);

  if (ret == ESP_OK) {
    SerialDebug.println(" successfull.");
  }  else  {
    SerialDebug.println("  failed. Error: " + String(esp_err_to_name(ret))); 
  }
  return ret;
} */

// Take and send a photo via Lora
void send_photo() {
  SerialDebug.println("send_photo()");
  camera_fb_t *fb; // Declare the variable for the pointer to the framebuffer

  if (cam_err == ESP_OK) {  // If the camera is ok
    SerialDebug.printf("  Taking picture: %d\n", imageID);
    setCpuFrequencyMhz(80); // Camera seems to need more than 40mhz to get a picture  TODO more research on lowering power here
    camera_enable_out_clock(&my_cam_config); // TODO Check result from this
    delay(1500);
    SerialDebug.printf("System Voltage: %d.\n", readV());
    fb = esp_camera_fb_get(); // Get the current frame buffer
    SerialDebug.printf("System Voltage: %d.\n", readV());
    delay(10);
    //esp_camera_deinit(); // Tried to see if this would allow us to power down the camera and power it back up again, it didn't.
    //camera_disable_out_clock(); // Saves about 10ma if we didn't turn the camera off anyway
    digitalWrite(PWDN_GPIO_NUM, HIGH); // Turn the camera power off, now need to reboot before taking next picture
    setCpuFrequencyMhz(CORE_FREQ);  // Reduce CPU frequency back to energy saving
    SerialDebug.printf("  Picture length: %d\n", fb->len);
    process_ssdv(fb);  // Main routine
    esp_camera_fb_return(fb);
  } else {
    SerialDebug.printf("WARNING: Camera Not Ok, but running process_ssdv anyway to send telemetry.\n");
    fb = 0;
    process_ssdv(fb);  // Main routine, run even if we dont have a picture as this is where we send location too.
  }
}

/* // Take and save a numbered photo to the SD Card
void save_photo_numbered() {
  SerialDebug.println("save_photo_numbered()");
  file_number++;
  SerialDebug.printf("Taking picture: %d\n", file_number);
  camera_fb_t *fb = esp_camera_fb_get();

  char *filename = (char*)malloc(21 + sizeof(int));
  sprintf(filename, "/sdcard/capture_%d.jpg", file_number);

  FILE *file = fopen(filename, "w");
  if (file != NULL)  {
    size_t err = fwrite(fb->buf, 1, fb->len, file);
    SerialDebug.printf("  File saved: %s\n", filename);
  }  else  {
    SerialDebug.printf("  ERROR: Could not open file: %s\n", filename);
  }
  fclose(file);
  esp_camera_fb_return(fb);
  free(filename);
} */

/* // take and save a dated photo to the SD Card
void save_photo_dated(){

  char strftime_buf[64];
  
  SerialDebug.println("save_photo_dated()");
  SerialDebug.println("  Taking picture...");
  camera_fb_t *fb = esp_camera_fb_get();

  time(&now);
  localtime_r(&now, &timeinfo);
  strftime(strftime_buf, sizeof(strftime_buf), "%F_%H_%M_%S", &timeinfo);

  char *filename = (char*)malloc(21 + sizeof(strftime_buf));
  sprintf(filename, "/sdcard/capture_%s.jpg", strftime_buf);

  FILE *file = fopen(filename, "w");
  if (file != NULL)  {
    size_t err = fwrite(fb->buf, 1, fb->len, file);
    SerialDebug.printf("  File saved: %s\n", filename);
  }  else  {
    SerialDebug.printf("  ERROR: Could not save file: %s\n", filename);
  }
  fclose(file);
  esp_camera_fb_return(fb);
  free(filename);
} */

/* // Call save_photo dated() or numbered()
void save_photo() {
  if (timeinfo.tm_year < (2016 - 1900) || internet_connected == false) { // if no internet or time not set
    save_photo_numbered(); // filenames in numbered order
  } else {
    save_photo_dated(); // filenames with date and time
  }
} */

// Setup the camera
esp_err_t camera_init() {
    //power up the camera if PWDN pin is defined
    if(PWDN_GPIO_NUM != -1) {
        pinMode(PWDN_GPIO_NUM, OUTPUT);
        digitalWrite(PWDN_GPIO_NUM, LOW);
    }

    setCpuFrequencyMhz(80); // Camera seems to need more than 40mhz  TODO more research on saving power here
    delay(10);
    
    esp_err_t err = esp_camera_init(&my_cam_config);  //initialize the camera

    delay(10);
    setCpuFrequencyMhz(CORE_FREQ);

    return err;
}


//#######################################################################################
// Main setup routine, runs once
void setup() {

  WRITE_PERI_REG(RTC_CNTL_BROWN_OUT_REG, 0); //disable brownout detector
  
  setCpuFrequencyMhz(CORE_FREQ); //reduce from 160 to save power
  
  SerialDebug.begin(115200);
  SerialDebug.println("\r\nsetup()");
  SerialDebug.flush();

  //while (1) {
    SerialDebug.printf("System Voltage: %d.\n", readV());
    delay(1000);
  //}

  // Help us to confirm we have the right config for the right board!
#if defined(BOOST)
  SerialDebug.println("  Boost Regulator."); SerialDebug.flush();
#elif defined (BUCK)
  SerialDebug.println("  Buck Regulator."); SerialDebug.flush();
#elif defined(NONE)
  SerialDebug.println("  No Regulator."); SerialDebug.flush();
#else
  SerialDebug.println("  ERROR: Incorrect regulator config"); SerialDebug.flush();
  delay(30000);
  ESP.restart();
#endif

/*
  // Test Frequency vs power
  int freq[] = {160,80,40,30,20,18, 16, 14, 12, 10, 8, 6, 4, 2, 1};
  for (int i = 0; i<sizeof freq/sizeof freq[0]; i++) {
    SerialDebug.printf("Frequency set to %d\n", freq[i]);
    setCpuFrequencyMhz(freq[i]);
    delay(5000);
  }
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
void loop()
{
  delay(1000);
  SerialDebug.println("main()");
  SerialDebug.flush();

  // Needed as if camera init fails in setup() we skip straight to loop()
  if (cam_err != ESP_OK) {
    SerialDebug.printf("ERROR: Camera init failed with error 0x%x\n", cam_err);
    digitalWrite(PWDN_GPIO_NUM, HIGH); // turn camera of!
  }

  send_photo();

  // Deep Sleep reset here to reset camera.  Allows us to turn the camera off as soon as we take a picture and then reboot to reinitialise it.
  // Dont reboot if below a certain voltage as we wont make it back (Brownout WDT kicks in before we can turn it off and we reboot loop).  
  // ESP32 module will run to about 2.15v if not rebooted
#if defined (BUCK) // If Buck dont reboot below this voltage
  if (readV() > 2700) {
#else
  if (readV() > 2500) { // If 2 x AA / AAA dont reboot below this voltage
#endif
    periph_module_reset(PERIPH_I2C0_MODULE);
    esp_sleep_enable_timer_wakeup(15 * 1000000l); // 1000000 us per Second
    esp_deep_sleep_start(); // Go into deep sleep for a legth of time to save power, and then reboot.
    ESP.restart(); // Should never get here
  } else {
    cam_err = -1; // Dont take any more pictures
    SerialDebug.printf("ERROR: Voltage below 2500mV, dont reboot or else we may not restart\n");
    digitalWrite(PWDN_GPIO_NUM, HIGH); // turn camera of!
  }

}

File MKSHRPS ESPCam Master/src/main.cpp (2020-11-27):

#define _MAIN_
#include <Arduino.h>
#include <esp_camera.h>
#include <WiFi.h>
#include <SPI.h>
#include <Wire.h>
#include <LoRa_LIB.h>
#include <Wire.h>
#include <TinyGPSPlus.h>
#include <main.h>

// Time
#include <time.h>
#include <lwip/err.h>
#include <lwip/apps/sntp.h>
// MicroSD
#include <driver/sdmmc_host.h>
#include <driver/sdmmc_defs.h>
#include <sdmmc_cmd.h>
#include <esp_vfs_fat.h>
#include <ssdv.h>

#define LORA_CSS  15   // will be 2,4 or 15 (Standard HSPI = 15) 

// The TinyGPS++ object
TinyGPSPlus gps;

// Edit ssid, password, capture_interval:
const char* ssid = "NSA";
const char* password = "orange";
int capture_interval = 15000; // microseconds between captures
//

long current_millis;
long last_capture_millis = 0;
static esp_err_t cam_err;
static esp_err_t card_err;
char strftime_buf[64];
int file_number = 0;
bool internet_connected = false;
struct tm timeinfo;
time_t now;

int t,n=0;
long frq = 434500000;
int counter = 0;
int loraBufferSize = 255;
bool firstRun = false;

// CAMERA_MODEL_AI_THINKER
#define PWDN_GPIO_NUM     32
#define RESET_GPIO_NUM    -1
#define XCLK_GPIO_NUM      0
#define SIOD_GPIO_NUM     26
#define SIOC_GPIO_NUM     27
#define Y9_GPIO_NUM       35
#define Y8_GPIO_NUM       34
#define Y7_GPIO_NUM       39
#define Y6_GPIO_NUM       36
#define Y5_GPIO_NUM       21
#define Y4_GPIO_NUM       19
#define Y3_GPIO_NUM       18
#define Y2_GPIO_NUM        5
#define VSYNC_GPIO_NUM    25
#define HREF_GPIO_NUM     23
#define PCLK_GPIO_NUM     22

// ssdv definitions
#define JPEG_RESOLUTION             4                                // 0-8 corresponfing to 320x240, 352x288, 640x480, 800x480, 1024x768, 1280x960, 1600x1200, 2048x1536, 2592x1944
#define JPEG_QUALITY                3                                // 0-16 corresponding to 96.7, 93.7, 87.3, 81.2, 74.8, 68.6, 62.3, 56.2, 50.0, 44.4, 39.9, 36.3, 33.2, 30.7, 28.5, 26.6, 25.8
#define SSDV_QUALITY                4                                // 0-7 corresponding to JPEG quality: 13, 18, 29, 43, 50, 71, 86 and 100
#define IMG_BUFF_SIZE               128                               // size of the buffer feeding SSDV process 
#define INTERLEAVE_TELEM            5                               // transmit a telemetry packet every X SSDV packets
#define LORA_BUFFER 255;

static esp_err_t init_sdcard();

static const char callsign[] = "MJS01";                    // maximum of 6 characters
uint8_t jpgRes                     = JPEG_RESOLUTION;
uint8_t jpgQuality                 = JPEG_QUALITY;
uint32_t imgSize                   = 0;
uint32_t imgCount                  = 1;
uint8_t ssdvQuality                = SSDV_QUALITY;
uint8_t imgBuff[IMG_BUFF_SIZE];
ssdv_t ssdv;
uint8_t loraBuff[256];
char tempStr[40];
char gpsMessage[256];

bool gpsSerialActive = false;

int imageID = 0;


int iread(uint8_t *buffer,int numBytes,camera_fb_t *fb, int fbIndex ){

  int bufSize = 0;
  // have we reached past end of imagebuffer
  if((fbIndex + numBytes ) < fb->len){
  
    bufSize = numBytes;
  }
  else{

    bufSize = fb->len - fbIndex;
  }
  // clear the dest buffer
  memset(buffer,0,numBytes);
  memcpy(buffer,&fb->buf[fbIndex],bufSize);
  return bufSize;
}


int checkGps(){
  //delay(1000);
  
  gpsSerialActive = false;
  while (Serial2.available() > 0){
    char dat = Serial2.read();
    gpsSerialActive = true;
    gps.encode(dat);


  }
  if(gpsSerialActive){
    Serial.println("gps serial active");
  }

  //  Serial.println("\n decoded GPS");
  
  if(gps.location.isUpdated()){

    if (gps.location.isValid()){
      GPS.Longitude = (float) gps.location.lng();
      GPS.Latitude = (float) gps.location.lat();
    }

    if (gps.altitude.isValid()){
      GPS.Altitude = (long) gps.altitude.meters();
    }

    // if gps data is ready
    if (gps.location.isValid() && gps.altitude.isValid()){
      GPS.isValid = true;
      //Serial.println("values valid");
    }

    
    if(gps.time.isValid() && gps.time.isUpdated() ){
    GPS.Hours = (uint8_t) gps.time.hour();
    GPS.Minutes = (uint8_t) gps.time.minute();
    GPS.Seconds = (uint8_t) gps.time.second();
    }

    /*
    if(GPS.isValid ){
      // get course and distance if we have a remote tracker

      GPS.courseTo =gps.courseTo(GPS.Latitude,GPS.Longitude,remote_data.latitude,remote_data.longitude);
      GPS.distancem = gps.distanceBetween(GPS.Latitude,GPS.Longitude,remote_data.latitude,remote_data.longitude);
      //remote_data.cardinalCourseTo = gps.cardinal(remote_data.courseTo);
    }
    */

  }
    GPS.Satellites = (unsigned int) gps.satellites.value();
    GPS.failedCS = (unsigned int) gps.failedChecksum();
    Serial.print("Satellites ");
    Serial.print(GPS.Satellites);
    Serial.print(" : failed chk ");
    Serial.print(GPS.failedCS);
}

char Hex(uint8_t index)
  {
    char HexTable[] = "0123456789ABCDEF";
    
    return HexTable[index];
  }


void buildPITSMessage(){
      
      //char gpsMessage[100];
      //char tempStr[40];
      // $$ ID, count, HH:MM:SS,Lat,lng,alt,Speed,Heading,sats,int temp,ext temp,pressure,humidity 
      strcpy(gpsMessage,"$$");
      strcat(gpsMessage,callsign);
      
      snprintf(tempStr,sizeof(tempStr),",%d,%02d:%02d:%02d,",GPS.flightCount,GPS.Hours,GPS.Minutes,GPS.Seconds);
      strcat(gpsMessage,tempStr);
      // convert using dtostrf() will convert float or double
      dtostrf(GPS.Latitude,2,6,tempStr);
      strcat(gpsMessage,tempStr);

      dtostrf(GPS.Longitude,2,6,tempStr);
      strcat(gpsMessage,",");
      strcat(gpsMessage,tempStr);

      ltoa(GPS.Altitude,tempStr,10);
      strcat(gpsMessage,",");
      strcat(gpsMessage,tempStr);

      snprintf(tempStr,40,",%d,%d,%d,%d,%d,%d,%d",GPS.Speed,GPS.Direction,GPS.Satellites,0,0,0,0);
      strcat(gpsMessage,tempStr);
      
      int Count = strlen(gpsMessage);

      unsigned int CRC = 0xffff;           // Seed
      //unsigned int xPolynomial = 0x1021;
      // do CRC calc and append to message
      for (int i = 2; i < Count; i++)
      {   
          CRC ^= (((unsigned int)gpsMessage[i]) << 8);
          for (int j=0; j<8; j++)
          {
              if (CRC & 0x8000)
                  CRC = (CRC << 1) ^ 0x1021;
              else
                  CRC <<= 1;
          }
      }

      gpsMessage[Count++] = '*';
      gpsMessage[Count++] = Hex((CRC >> 12) & 15);
      gpsMessage[Count++] = Hex((CRC >> 8) & 15);
      gpsMessage[Count++] = Hex((CRC >> 4) & 15);
      gpsMessage[Count++] = Hex(CRC & 15);
      gpsMessage[Count++] = '\n';  
      gpsMessage[Count++] = '\0';
  
      //Serial.println(gpsMessage);
  }
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

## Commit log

2020-12-08 Commit post first flight
    [ESP32-Cam-Pico-V4.brd, ESP32-Cam-Pico-V4.sch, Float1e.xls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]
2021-01-18 Pre Flight 2
    [Wedge.scad, Wedge.stl, Wedge2.stl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]
2021-01-23 Flight 2 done
    [AllTelem.xlsx]
2021-02-14 Minor updates
    [Float1e.xls, WedgeMulti.stl, WedgeMulti_stl.scad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]
2023-02-17 Moved to own repo
    [Float1e.xls]
2023-02-17 Moved to new repo
    [burst3.xls]

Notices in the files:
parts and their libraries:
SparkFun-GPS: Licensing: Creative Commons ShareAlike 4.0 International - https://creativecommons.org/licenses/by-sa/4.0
